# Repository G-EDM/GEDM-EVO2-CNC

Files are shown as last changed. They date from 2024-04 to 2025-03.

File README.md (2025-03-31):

# Schematics, Gerber files and Kicad projects for the PCBs
[>>> Schematics, Gerber files, Kicad projects and PCBway links <<<](https://github.com/G-EDM/GEDM-EVO2-CNC/tree/main/files/schematics-and-gerbers)
</br>
</br>

# GEDM-EVO2-CNC
Gantry based 3 axis CNC router with heavy duty 3d printed parts

```diff
  ______         ________ _______  __       __      ________ __     __  ______       ______ ______ 
 /      \       |        \       \|  \     /  \    |        \  \   |  \/      \     |      \      \
|  ▓▓▓▓▓▓\      | ▓▓▓▓▓▓▓▓ ▓▓▓▓▓▓▓\ ▓▓\   /  ▓▓    | ▓▓▓▓▓▓▓▓ ▓▓   | ▓▓  ▓▓▓▓▓▓\     \▓▓▓▓▓▓\▓▓▓▓▓▓
| ▓▓ __\▓▓______| ▓▓__   | ▓▓  | ▓▓ ▓▓▓\ /  ▓▓▓    | ▓▓__   | ▓▓   | ▓▓ ▓▓  | ▓▓      | ▓▓   | ▓▓  
| ▓▓|    \      \ ▓▓  \  | ▓▓  | ▓▓ ▓▓▓▓\  ▓▓▓▓    | ▓▓  \   \▓▓\ /  ▓▓ ▓▓  | ▓▓      | ▓▓   | ▓▓  
| ▓▓ \▓▓▓▓\▓▓▓▓▓▓ ▓▓▓▓▓  | ▓▓  | ▓▓ ▓▓\▓▓ ▓▓ ▓▓    | ▓▓▓▓▓    \▓▓\  ▓▓| ▓▓  | ▓▓      | ▓▓   | ▓▓  
| ▓▓__| ▓▓      | ▓▓_____| ▓▓__/ ▓▓ ▓▓ \▓▓▓| ▓▓    | ▓▓_____   \▓▓ ▓▓ | ▓▓__/ ▓▓     _| ▓▓_ _| ▓▓_ 
 \▓▓    ▓▓      | ▓▓     \ ▓▓    ▓▓ ▓▓  \▓ | ▓▓    | ▓▓     \   \▓▓▓   \▓▓    ▓▓    |   ▓▓ \   ▓▓ \
  \▓▓▓▓▓▓        \▓▓▓▓▓▓▓▓\▓▓▓▓▓▓▓ \▓▓      \▓▓     \▓▓▓▓▓▓▓▓    \▓     \▓▓▓▓▓▓      \▓▓▓▓▓▓\▓▓▓▓▓▓
```

# Downloadlinks for the freecad files
    The router file is a little crappy. The extrusions/tank/rails of the frame are not a the correct position and the Y ballscrew is too short etc.
    But it can be used

[>>> G-EDM EVOII Wire extension FreeCAD Project <<<](https://drive.google.com/file/d/1ZBrTBwRvTHIMtCySQIoWtpVMdJbfWR3E/view)
</br>
[>>> G-EDM EVOII Router FreeCAD Project <<<](https://drive.google.com/file/d/1OkYVYsVrToy4-q0G6XMzgWKsSyYXRRj4/view)
</br>
</br>

# Responsible for the content provided
    Lautensack Roland (Germany)
    Contact: goblin-dev@proton.me

# This project is still a work in progress and not fully finished yet

The GEDM-EVO2 Gantry Router uses heavy duty 3D printed parts, strong HGR20 linear rails, ballscrews and heavy profiles (40x160).

With only a few upgrades/changes it will be able to not only do EDM but also mill wood and smaller aluminum parts.

In order to do those milling jobs it may require a second ballscrew on the left side.

The wire extension used in the images is the one designed by Alex Treseder for the PicoEDM:
https://github.com/alextreseder/picoEDM

Not fully finished. Z axis is still missing and the massive aluminum plate on the front is temporary.

Check out the youtube channel:
Cutting stainless steel demo (https://youtu.be/4GycnoLOGnc)

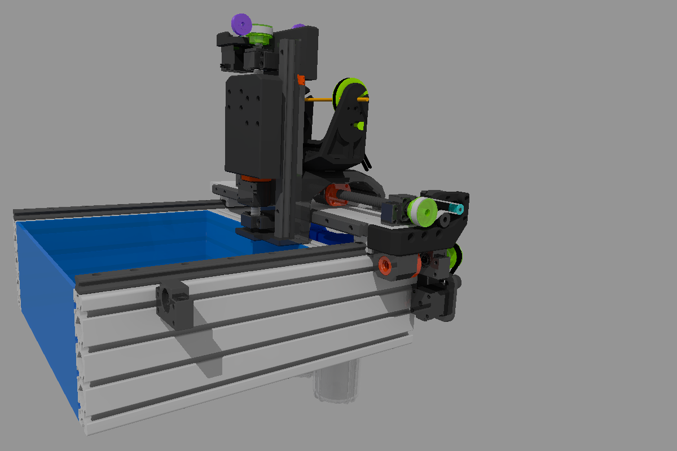
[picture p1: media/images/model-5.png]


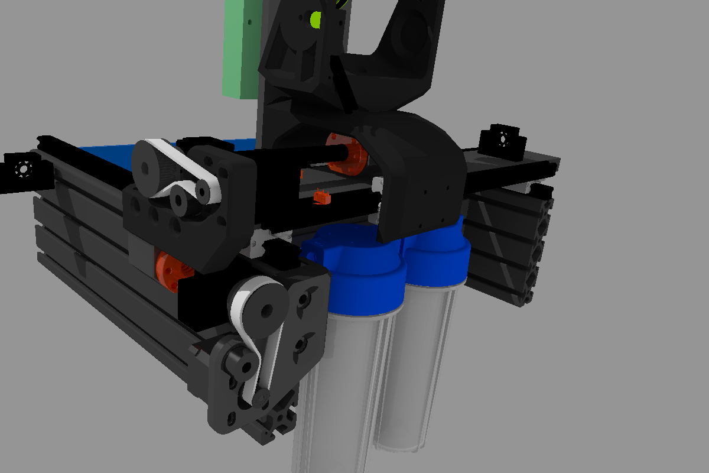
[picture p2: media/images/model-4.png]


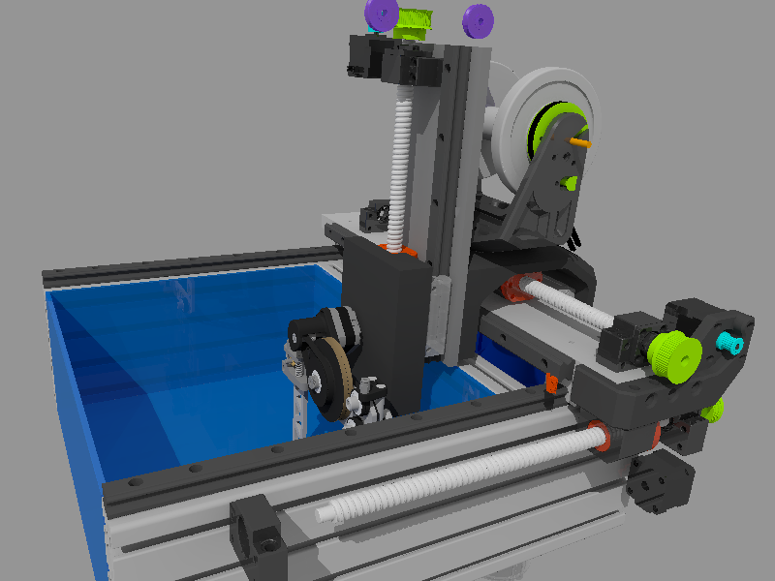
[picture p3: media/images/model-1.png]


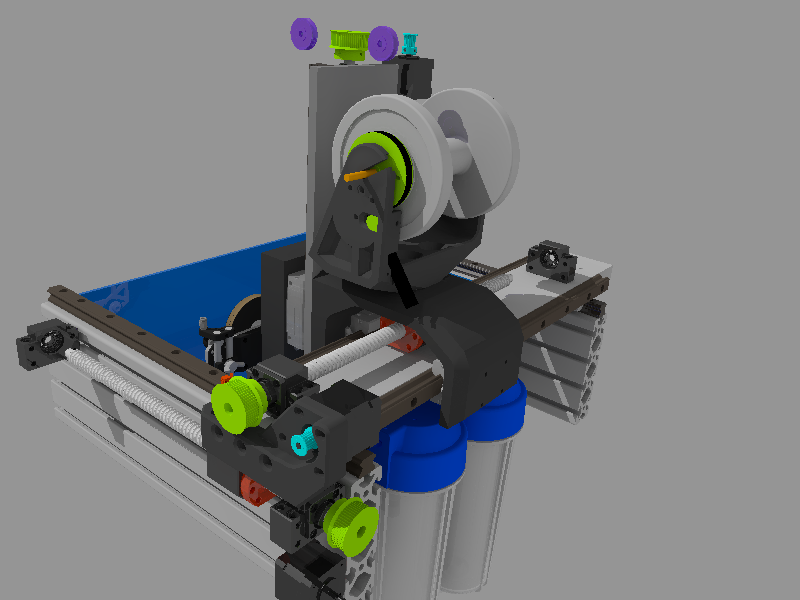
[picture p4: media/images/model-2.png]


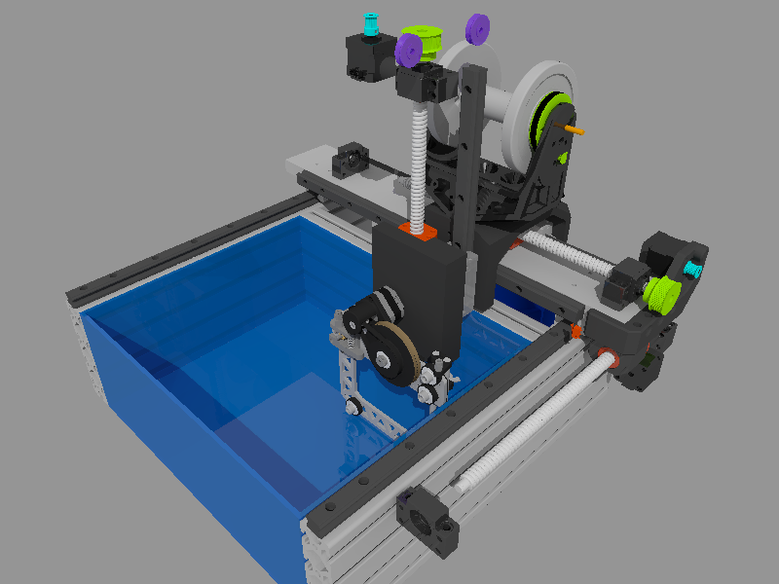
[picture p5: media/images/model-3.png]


# Legal notes

    The author of this project is in no way responsible for whatever people do with it.

    No warranty. 

# License

    All files provided are for private use only if not declared otherwise and any form of commercial use or redistribution of the protected files is prohibited. 

# Follow the project:

[>>> Follow the project on Youtube <<<](https://www.youtube.com/@G-EDM/videos)

[>>> Stay informed on Hackaday <<<](https://hackaday.io/project/190371-g-edm)

[>>> Get involved on Discord <<<](https://discord.gg/9cTsyDkEbe)

# Donations

    * Developement is not always as fast as it could be if you're poor. You want to donate something? 
    * Paypal: paypal.me/gedmdev
    * Bitcoin: bc1qkz8vwrd3pupewdtyg09qj9nv249vlgdy4ffhyv
    


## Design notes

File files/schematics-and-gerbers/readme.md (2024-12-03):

# Update

Added the new EVOIII PCB. This board was designed for easier manufacturing and is a replacement for the sensorboard and the pulseboard. It has both integrated on a single PCB.

The PCBs can be ordered on PCBway using following links:

# Motionboard
https://www.pcbway.com/project/shareproject/G_EDM_Low_budget_DIY_Wire_EDM_machine_34e1e043.html

# EVOIII Board (Sensorboard and Pulseboard on one PCB)
https://www.pcbway.com/project/shareproject/G_EDM_EVOIII_board_Low_budget_DIY_Wire_EDM_machine_482d5b7a.html

<br/><br/><br/><br/>
# If the EVOIII board is used the following two PCBs are not needed.
<br/><br/>

# Sensorboard (Not needed if the EVOIII board is used)
https://www.pcbway.com/project/shareproject/G_EDM_Low_budget_DIY_Wire_EDM_machine_sensorboard_24b74366.html

# Pulseboard (Not needed if the EVOIII board is used)
https://www.pcbway.com/project/shareproject/G_EDM_Low_budget_DIY_Wire_EDM_machine_pulseboard_8975f488.html

The full electronic enclosure contains the control panel with the ESP32 motion controller and a touch screen and the spark generator.

The pulseboard and the sensing unit are two dedicated PCBs stacked on top of eachother.

The sensing unit is not bound to the G-EDM pulseboard and can be used with a custom generator as well.

Currently only the schmeatics of the pulseboard PCB is uploaded here.

Sennsing unit / motionboard and gerber files will follow.

The pulseboard can be used as stand-alone board too but the sensing is not comparable to the new sense circuit that is able to capture raw watercontact and even the tiniest discharges.

Files currently provided:

Schematics:
```diff
+ Pulseboard EVO² - yes
```
```diff
+ Sensing Unit EVO² - yes
```
```diff
+ Motionboard EVO² - yes
```

Gerber files:
```diff
+ Pulseboard EVO² - yes
```
```diff
+ Sensing Unit EVO² - yes
```
```diff
+ Motionboard EVO² - yes
```

BOM:
```diff
+ Pulseboard EVO² - yes
```
```diff
+ Sensing Unit EVO² - yes
```
```diff
+ Motionboard EVO² - yes
```

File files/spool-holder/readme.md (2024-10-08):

# Note

The belt dampener doesn't work very well. The belt starts to increase tension over time and the spool motion is not smooth.

But there is an easy fix for now:

1. Fully remove the belt
2. Add one washer+lockwasher+washer to each side of the screws holding the spool (left/right)
3. Adjust the tension using those screws

Also mount the spool flipped by 180° and bring the spool more forward by skipping the back mounting screw row and only use the two front screws to mount it.

Images: https://github.com/G-EDM/GEDM-EVO2-CNC/tree/main/files/spool-holder/images/spool-bug-fix

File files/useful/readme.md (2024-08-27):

# Adapters to mount the shunt to the cube
# Little drill helper with the hole pattern of the cube

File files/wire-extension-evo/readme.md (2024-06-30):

The current contact I use is this one:
[EDM Maschine für S010-1 ](https://www.ebay.de/itm/276514273684)

40mm x 10mm x 5mm
https://de.aliexpress.com/item/1005007089428164.html

There are multiple screw holes that can be used to mount other contacts too or build a custom contact.

How to build it:
https://www.youtube.com/watch?v=NhJeJGdWdE0

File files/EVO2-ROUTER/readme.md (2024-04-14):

# Work in progress

This folder is not complete and may miss some files.

Missing files are mostly Z axis and build tutorial related.

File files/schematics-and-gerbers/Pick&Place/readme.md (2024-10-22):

# WARNING!!!

This is currently a work in progress to provide files for PCBA (Assembly) services.

It is not finished yet and needs validation and testing first.

The BOMs only contain the SMD parts and not the through hole parts.

There are some problems figuring out the correct footprints for the ICs. Every manufacturer names things different and it is a total mess.
In the end there are all kinds of footprints labeled as for example SOP-8 but have massive difference in size.
Then there is SOIC-8 which seems to be the same as "some" SOP-8 etc.

Industry messed this up badly and I have to sort this out first.

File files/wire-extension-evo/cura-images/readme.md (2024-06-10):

The support settings shown are just the ones I used. Printer is an Ender3 v2 with MGN12 linear rails and BLtouch sensor for auto bed leveling.

The printposition of the parts needs to be as shown on the images.

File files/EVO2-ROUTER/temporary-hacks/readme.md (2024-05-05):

# This is just a temporay solution 

The files included in this folder are personal hacks to get the wire extension mounted without using the final Z axis. This folder will be removed once everything is finished!

It is not perfect but it will get some stuff done.

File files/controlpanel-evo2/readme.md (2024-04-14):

This folder includes the raw freecad project file for the panel too.

# License

    All files provided are for private use only if not declared otherwise and any form of commercial use or redistribution of the protected files is prohibited. 

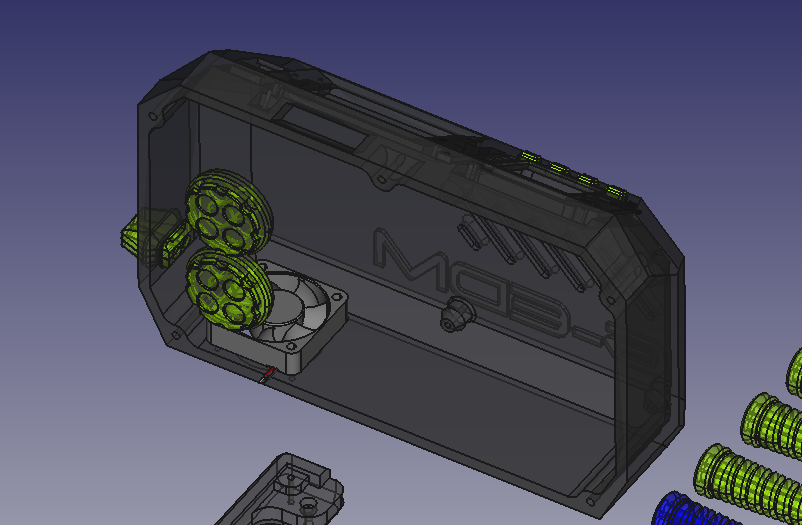
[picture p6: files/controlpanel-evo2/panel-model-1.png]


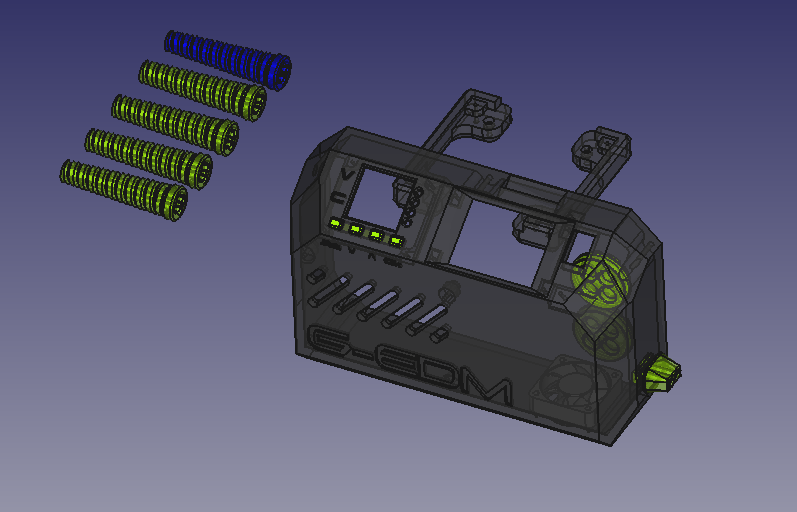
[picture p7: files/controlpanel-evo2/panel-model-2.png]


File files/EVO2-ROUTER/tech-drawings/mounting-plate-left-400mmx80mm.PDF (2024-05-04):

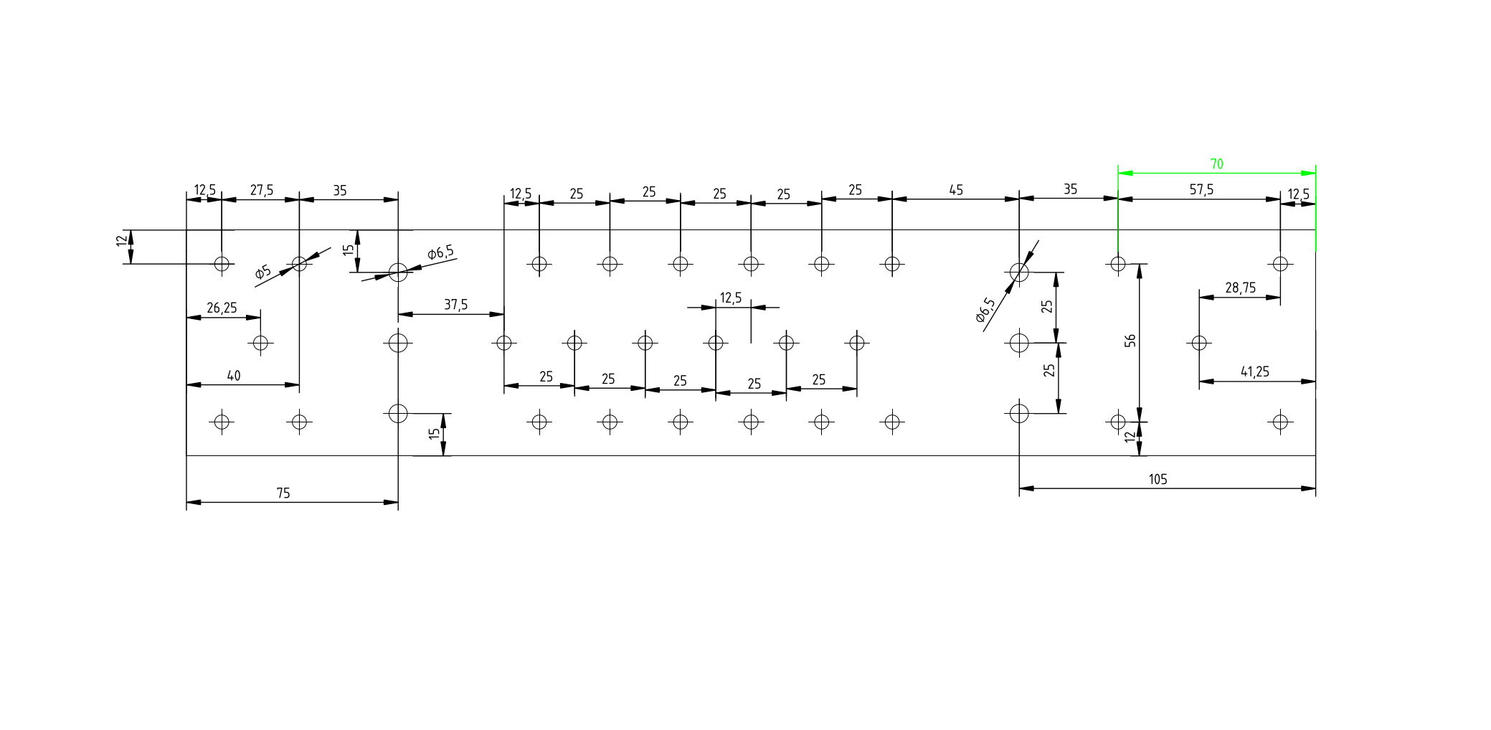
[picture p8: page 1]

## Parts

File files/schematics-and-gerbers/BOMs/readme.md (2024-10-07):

# Warning:

No warranties. The BOMs may contain errors or miss parts. I have done them really quick without deeper review.

Some parts of the BOM are using the discount price if 10 pieces are bought. Nobody buys 1 0805 SMD resistor etc.

Sensorboard: 57,17.- (Euros)
Motionboard: 13,80.-
Pulseboard: 41,25.-

112.25.- for the PCB components without taxes. 
134.65 with tax

PCBway has a minimum order of 5 PCBs per board. A full set ordered from PCBway would contain:
     5 Motionboards
     5 Sensorboards
     5 Pulseboards

Cost with tax and shipment for the 15 PCBs:
     175.77.- (Euros)

Per Set (One of each boards):
     35.154.-
     
Total for One populated Set of boards:
    169.80.-

Other parts needed: JST male connectors, wires etc are not calculated yet. 
ESP32 and TMC drivers are not included in the motionboard BOM

There are other parts needed like:

M3 Hex spacer M3*26mm
https://www.ebay.de/itm/166217190652

M3 Washers and screws

22AWG silicone wire black/red

JST XH crimpset

And maybe some other stuff. Read the manual:
https://www.youtube.com/watch?v=dQw4w9WgXcQ

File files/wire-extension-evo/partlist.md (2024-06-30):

This partlist is a work in progress and may miss some parts like the exact amount of washers and maybe a screw too. The small V bearings may need two washers to prevent them from rubbing. They are not build very rigid and have some play. 

##### Tools #####
M10 tap (to make the thread for the flushing tube fittings)
An Allen Wrench set 
10mm hex nut key (to screw the flushing fitting in)
A small micro gas blow torch to postprocess some of the printed parts. Remelting outer layers and screwholes to make them more solid.

If possible use stainless screws/nut/washers. Normal steel will rust fast.

##### Filament #####
2 spools PLA+ (eSun is very good)
A few grams TPU to print the flushing nozzle seals

##### Current contact #####
    The are different holes that can be used to mount other/custom contacts too.
    S010-0 current contact; 40mmx10mmx5mm
    https://de.aliexpress.com/item/1005007089428164.html
    https://www.ebay.de/itm/276514273684

##### Screws #####

     ### M3 ###  
     4x M3x12mm (for spool motor) 
     2x M3x14mm 
     2x M3x18mm (20mm is ok too)
     1x M3x20mm
     2x M3x25mm
     2x M3x30mm
     2x M3x5mm setscrews (8mm length is ok too)

     ### M5 ###
     6x M5x30mm
     2x M5x35mm
     2x M5x8mm setscrew (can be longer too)

     ### M6 ###
     1x M6x25mm
     2x M6x30mm 
     2x M6x35mm
     3x M6x40mm
     2x M6x50mm
     3x M6x55mm (60mm works for those too)
     4x M6x60mm

##### Hexnuts #####

    12x M3
    10x M5
    14x M6
    
    ##### selflocking #####
    1x M3
    3x M6

##### Washers #####

    11x M3
    6x M5
    14x M6

##### Slide bearings #####

    4x 12mm OD x 10mm ID x 10mm Length
    https://www.amazon.de/sourcing-map-Gleitlager-umwickelte-%C3%96lbarren/dp/B07KQ5RSJW

##### Bearings #####

The big bearings body is from stainless and will not rust but the balls inside will rust very fast. After the first use the bearings have water inside and it takes only one or two days for the bearing to fully block if not moved daily. It is ok to remove one ball from the bearings. Even if the bearings will have a little play it prevents them from getting stuck. The best way is to replace the balls with ceramic balls. This combination would last very long.

3x V623ZZ 3x12x4mm bearings (v-groove)
https://www.amazon.de/St%C3%BCck-V623ZZ-V-Nut-Kugellager-Riemenscheibe-Schienen-Linearbewegungssystem-3x12x4mm/dp/B08K95KNFR

7x 696-2RS Kugellager sealed 6x15x5mm 
https://www.amazon.de/dp/B09V5DBM6Y

5x v groove bearing "Cnbtr" 6x30x8mm (2.5mm groove depth. They are sold as 8mm width but the center is 9mm and only the outer ring is 8mm. Integrated washers)
https://www.amazon.de/dp/B076VCCCMS

##### Rails #####

2x 10mm x 180mm precision roundbar in stainless steel
https://www.amazon.de/Pr%C3%A4zisionswelle-10mm-geschliffen-geh%C3%A4rtet-ZUSCHNITT/dp/B07GNG1Y3Z

##### Others #####

1x small Banana plug socket with M6 thread (The little panel can be modified to fit other sockets too)

2x Pneumatic fittings with M10 thread
https://www.amazon.de/dp/B07DGLCJ4Z

2x V5/V6 3D printer nozzle in stainless steel or tungsten with the size of the wire
https://www.amazon.de/PREMIUM-Nozzle-0-25mm-Edelstahl-Stainless/dp/B0CNWG1KYZ

##### Not specified yet #####

1x banana socket
2x springs
4mm OD hydraulic tube
EDM current contact

##### Printsettings #####

Print inner walls first!

Most parts have supports touching buildplate only. This is important for the big main body and the upper/lower guides as there is no way to remove the supports from the internal routing. Printing throughholes and hexnutslots with the edge to the top works without problems.

The big parts should have supports on the outer chamfers too while this is not needed for smaller parts. So some parts have a support angle <45° while the ones that don't need chamfer supports do ha ve a support angle >45°. For the parts without chamfer supports just set it to 50°.

The motor shaft is printed without any supports. 

Postprocessing:

There are four parts that need heat postprocessing to increase the strength. The wire tensioner A and B and the wire follower and alos the motor shaft.

The motor shaft is easy to refine. First insert the hexnuts. The heating will shrink the part. 

Put a screw into it, plug it onto a drill and heat it up. Step by step. First the circular/smooth area, then cool it with water, Then the middle torque connection area and again cool it and then a tiny sensitive and short heating on the thread. Really just a super short amount of time.

After that use sandpaper to smoothen the circualr area. Rough grid and then fine grid. Then use a M5 screw to enlarge the hole for the stepper shaft. Using a screw seems to be more carefully then a drill. The thing should sit tightly on the stepper even without the setscrew locking it.

Same heattreatment for the wire tensioners and wire follower. Put the bearings in first to prevent shrinking and then do the outer part. A little deformation is ok. Those parts don't need high precision. Don't do the full part in one pass. Step by step and leting it cooldown again between steps.

If the plastic burns or smokes it is done wrong. There are two ways. One is to move the ligther fast and constant to slowly heat the area. But this will certainly burn the part sometimes. Another is to place the part close to the side of the flame until it gets glossy. This works with a normal lighter too and will give a nice result without much risk for overheating but will take much more time to make.

Printsettings for the big wire module (main body and connector):

Those settings will create a harder to remove support structure! Postprocessing will take more time.
This settings are only used for heavy duty parts.
Add a thick layer adhesive to the Ender3v2 printbed. I used hairspray but that may not work for everyone.. Use an adhessive that works for the build plate of the printer.

Layer height: 0.3mm
Walls: 14 (wall print order: inner walls first for better overhangs)
Top/Bottom layers: 12
Temperature: 230° for eSun PLA+

Print Speed: 50mm/s (Warning: Those are the settings I used to create the gCode. But I changed the speed on the printer to 80% of those settings)
    Infill: 50mm/s
    Outer Walls: 25mm/s
    Inner Walls: 30mm/s
    Top/Bottom: 35mm/s
    Support Infill: 25mm/s
    Support Interface: 35mm/s
    Travel Speed: 100mm/s
    Brim: 20mm/s

Infill: 
    Density: 70% 
    Pattern: Lines
    
Support:
    Structure: Normal
    Placement: Touching Buildplate
    Overhang Angle: 20°
    Pattern: Lines
    Density: 20%
    Z-Distance: 0.2mm
    X/Y Distance: 0.3mm
    Priority: Z overrides X/Y
    Enable Support INterface: All yes
    Support Interface Thickness: 2mm for all
    Support Interface Density: 26.333%
    Support Interface Pattern: Lines
    
Adhesion:
    Build Plate Adhesion Type: Brim
    Brim Width: 12mm
    Brim Replaces Support: Yes

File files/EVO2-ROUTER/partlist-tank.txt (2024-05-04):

Acrylic glass:
    1x 430x429x8mm
    2x 420x152x5mm
    2x 429x152x5mm
    
    4x 50x50x50mm acrily block to mount the stainless plate (Warning: The blocks are cutted from a thick plate/bar and the sides that are cut are most fo the time not accurate. Measure the block to find the accurate top/bottom. )
    
Glue:
    1x Solvent (S-PolyBond® or similar. Viscosity like water)
    1x Glue (Acrifix 1R 0192 or similar. Thicker glue fro acrylic used to seal the inner edges. Acrifix 0192 is UV reactive. It smells like hell and without a UV lamp it takes long to harden. A small UV pocket lamp is ok. If no UV lamp is available put the part into the sun. It does dry with room light too but takes very long and keeps smelling everything up. Acrifix 0190 is the non UV version.)

Stainless steel plate:
    1x 400x80x6mm

Fittings for the hose:
    2x 3/4" Female 1" Male Brass Bulkhead Fitting
    1x 3/4" 13mm barbed brass hose fitting with outer thread (screwed into the big fitting)
    
    In germany there are sets available: https://www.ebay.de/itm/193008996748
    
Hose:
    12mm ID hose.
    
Pump:
    12v pump, 1000l/min, 30w https://www.amazon.de/gp/product/B0C3Q887C5
    The pump in the link does not ship with hose fittings! If you get this specific model it needs two 1/2" barbed fittings with inner thread.

Filter:
    2 stage RO water filter. One stage with an activated carbon filter and the other sage with a 5 micron sediment filter.
    https://www.amazon.de/Naturewater-Wandhalterung-Filterschl%C3%BCssel-Sedimentfilter-Aktivkohleblock/dp/B008U8BY90
    
    Depending on the filter you buy it may need another set of barbed fittings. This time with outer thread.

Build tips:

    Using the watery solvent is not easy. Good luck.
    
    I used the solvent to get the box together and then just poured solvent into the inner edges while having the box tilted. This way the solvent will suck into the joint where the connection is not done. Don't wait with this too long and do this as soon as the box can be moved without falling apart which happens fast.

    If the solvent drops onto the acrylic don't wash it away. Let it vaporize! It will leave cloudy marks that later can be get rid of with a small lighter blow torch. Just blow torch it with a constant motion until it is transparent again. Same can be done with the edges of the box.
    
    One thing to keep in mind while flame polishing acrylic is that it creates stress in the plate. If solvent touches a flame polished surface it will instantly start to create cracks in the surface. In theory it is better not doing it and keep the milky spots.
    
    Using some sandpaper to round the edges and then blowtorch them shiny.

    After the solvent vaporized and the box is stable the inner joint needs to be sealed. Tilt the box and fill the joint with the glue in a straight line. Let it crawl into the joint, give it some time to rest and then go one to the next edges. Process is repeated multiple times to have a strong and thick seal on every joint. Give it a little time between each pass to let it dry a little bit.

    To drill the big hole I used a step drill bit and some smaller drills to predrill the initial hole.
    
    The step drill bit was a little too small so after having the main hole drilled I placed the fitting into the hole and used the small blow torch to heat it up until it started to soften the plastic. Do this carefully and step by step.
    
    After the fitting is in place remove the plastic from the edges and clean the hole.
    
    To get a really flat surface insert the fitting without gaskets, screw it tight and then heat the fitting from the inside again. It will align itself in place.
    
    Remove the hot fitting as soon as possible and also use a large M8 hex key to work with the hot fitting and prevent it from tilting.

    The brass fitting will be too hot to handle with bare hands and it will take long until it cools down.

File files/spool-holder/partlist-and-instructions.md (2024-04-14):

1x M4x16
1x M6x35
1x M6x45
2x M3x40 (min 30mm)
1x M3x16
2x M3x20 (larger is ok too)

2x Hexnut M6 (self locking! Important!)
2x Hexnut M3

Ballbearing 15x6x5 (OD 15mm; ID 6mm; 5mm height)

6mm GT2 belt (open ended)

Print tips:

Spool holder main can be printed with 25% infill and 5 walls.
It is a big part and it is highly recommended to add some adhesive to the build plate. I use 
strong hairspray. Lots of it.

All other PLA+ parts are printed with 100 infill.

The TPU ring is printed with 1 wall and 20% infill to keep it soft.

Build tips: 

Use a stormlighter to heat screws and screw them in hot where needed to create the threading. Same process sued for hexnuts too. 

It is also recommended to carefully use a stormlighter on the big part and re-melt the outer layers at critical position. Needs to be done carefully and fast to not burn the plastic or create burned spots. This increases the average strength heavily.

If the adapter is hard to put into the spool just put an M6 screw into a drill, screw the adapter on it and sand it down until it fits.

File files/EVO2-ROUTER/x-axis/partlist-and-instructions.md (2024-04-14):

1x 500mm 1605 SFU ballscrew with SF12 / SK12 bearing blocks and a DSGH16H nut housing
2x 500mm HGR20 linear rail
2x HGH20CA linear block

Note: Most sets of linear rails ship with 2 blocks per rail. We don't need to blocks per rail and it is possible to just take one 1000mm rail with two block and cut it into two 500mm rails.

1x Aluminum plate 600mm x 85mm x 20mm (best is to have grinded surface and a precision cut; The cut needs to be very very parallel!)

1x M3 to M6 flat washers and lock washers (a set or jsut a bunsh of them for eevery size)

Screws:

4x M6x30mm (To mount the spoolholed onto the slide)
4x M5x12
8x M5x20
4x M3x (to mount the Nema17)
1x M8x (to mount the belt tensioning bearings)
2x M3x12 (to tighten the big pulley)
2x M3 setscrew (to tighten the small pulley)
3x M6x (to mount the motor bracket onto the portal plate)
1x M5x (to mount the motor bracket onto the portal plate)

2x M6x (for the BF12) // If you don't have good tools and use a hand drill I recommend to mount those bearings with M5 instead of M6. Using M5 gives some more room for misalignment while drilling)
4x M6x (for the BK12) // If you don't have good tools and use a hand drill I recommend to mount those bearings with M5 instead of M6. Using M5 gives some more room for misalignment while drilling)

4x M5x (for the DSGH16H)

Hex Nuts:

A bunsh of M6 hex nuts (just a few, maybe 10)
A bunsh of M3 hex nuts (just a few for the pulleys needed. Maybe 4)

2x Ball bearings 608ZZ 8mmx22mx7mm (height can be more than 7mm too. Even with two bearings it is a tight fit for the belt on the edge.)

10mm GT2 belt (closed; length not determined yet)

Print tips:

The big XZ slide needs to be printed laying on the left side. Normal supports touching buildplate only and 30° support overhang angle.
A Brim is also needed. I used a 15mm Brim.
Another important thing is to spray the printbed with some kind of adhesive. Strong hairspray works for Ender3v2 printbeds. A lot of it.

The part is heavy duty and consumes almost an entire spool. Travelspeed should be reduced. My ender is modified with MGN12 lienar rails and used 110mm/min for travels. 
Layerheight can be 0.3mm. My print took <50 hours.

Build tips:

After the part is finished it is recommened to increase the average strenght with the help of remelting.
At least the holes need to be remeleted. Bolting M6 screw tightly can easily split the layer apart. To do so just use a small blowtorch and heat up the inner holes.

I remelted the full outer part but this will shrink the part heavily and needs to be done carefully.

Mount the part first to prevent the shrinking from respotioning the holes etc too much. Then blowtorch along the part fast and until the surface gets glossy.
Don't do this with the full part at once. Surface after surface and in between letting it cool down.

To give it a nice matte finish the part can then get a little sanding.

Some holes may need to be drilled to size after printing and if something does not fit well it is possible to use a soldering iron to change the hole positions.

If there is too much resistance in the ballscrew it is also possible to soften the back and/or top of the slide to release the stress and force it into a perfect fit.

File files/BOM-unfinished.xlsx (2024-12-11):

 |  | G-EDM BOM Extra
Item # | *Qty | Manufacturer | *Mfg Part # | Description / Value | Comments | Euros total
1 | 1 |  | ILI9341 Touch Display; SPI; 2,4“; 240x320; XPT2046 (Touch controller); | There are many different version available. Those two fit in the panel and work: https://www.amazon.de/ILI9341-240x320-Display-Touch-Arduino/dp/B07YTW28FB https://www.ebay.de/itm/145884439469
2 | 2 | Az-delivery | ESP32 NodeMCU Module WLAN WiFi Development Board | Dev Kit C V2 with CP2102; 38 Pins | https://www.az-delivery.de/en/products/esp32-developmentboard
3 | 1 |  | On/Off rocker switch; 2 pole; Normally Open; 9x13mm | https://www.amazon.de/Mini-Wippenschalter-Wippschalter-Kippschalter-Ger%C3%A4teschalter-rechteckig/dp/B0CCCBLXCS
4 | 4 |  | ST42STH47-1684A | Nema 17; 0.4Nm; 1.68A; 1.8° Step angle; Rated 2.8v; https://eu.robotshop.com/de/products/nema-17-schrittmotor-sy42sth47-1684a-einzelwelle |  | 88.-
5
6 | 1 |  | DPH8909 (TTL) | DPH8909 Programmable DC Power Supply CC CV TTL Communications Output 0-9.6A os12 https://www.ebay.de/itm/355082474892 | TTL version! Not the RS or RF version. The DPM8605 is half the price and works too but has a max output voltage of 60V and the input voltage needs to be set below 70V | 110.-
7 | 1 |  | 0-80V variable PSU; 6A480W | https://www.amazon.de/Transformator-Dual-Digital-Anzeige-Schaltnetzteil-Drehzahlregelung-wissenschaftliche/dp/B0BQ33XG33 |  | 56.-
8 | 1 |  | 12V 10A PSU | https://www.amazon.de/Kingwei-Schaltnetzteil-Netzteil-Transformator-Streifen/dp/B08QCNYLY8 |  | 18.-
9 | 1 | Mean Well | MEAN WELL PSU APV-35-12, 12 V-/3 A | https://www.amazon.de/MEAN-WELL-Schaltnetzteil-APV-35-12-12/dp/B083QNC9XG |  | 17.-
10 | 4 |  | TMC2209 Stepper driver with big heatsink | https://www.amazon.de/WANGCL-Schrittmotor-Treiber-K%C3%BChlk%C3%B6rper-hervorragende-Stummschaltung/dp/B0B1MM4BKH |  | 28.-

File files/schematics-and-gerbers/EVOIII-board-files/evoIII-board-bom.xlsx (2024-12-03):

 |  |  | G-EDM EVOII Sensorboard – BOM
Item # | *Designator | *Qty | Manufacturer | *Mfg Part # | Description / Value | *Package/Footprint | Type | Comments
16 | C31,C32,C23,C22 | 4 | KEMET | C0805C101J5RACTU | Multilayer Ceramic Capacitors MLCC - SMD/SMT 50V 100pF X7R 0805 5% | C_0805_2012Metric_Pad1.18x1.45mm_HandSolder | SMD
2 | C1,C3,C6,C8,C10,C13,C16,C18,C20,C27,C30,C35,C36,C37,C38,C39,C40,C45,C46 | 19 | KYOCERA AVX | 08055C104K4T2A | Multilayer Ceramic Capacitors MLCC - SMD/SMT 50V 0.1uF X7R | C_0805_2012Metric_Pad1.18x1.45mm_HandSolder | SMD
36 | C25,C24 | 0 |  | DNP | DNP | C_0805_2012Metric_Pad1.18x1.45mm_HandSolder | SMD | DNP
39 | C11,C29 | 2 | Murata Electronics | GRM32RR71H105KA01K | Multilayer Ceramic Capacitors MLCC - SMD/SMT 1 uF 50 VDC 10% 1210 X7R | C_1210_3225Metric_Pad1.33x2.70mm_HandSolder | THT
15 | C2 | 1 | KYOCERA AVX | 12107A101JAT2A | Multilayer Ceramic Capacitors MLCC – SMD/SMT 500V 100pF | C_1210_3225Metric_Pad1.33x2.70mm_HandSolder | SMD
4 | C28,C33,C44,C43 | 4 | Panasonic | EEEHA1C470WR | Aluminium Electrolytic Capacitors - SMD 16V 47uF | CP_Elec_5x5.4 | SMD
5 | C12,C15,C17,C21 | 4 | Panasonic | EEE-HAV221UAP | Aluminium Electrolytic Capacitors - SMD 220UF 35V | CP_Elec_8x10.5 | SMD
43 | C7 | 1 | Panasonic | EEE-HAC221XAP | Aluminium Electrolytic Capacitors - SMD 220UF 16V HA SMD | CP_Elec_6.3x7.7 | SMD
35 | R30,R31 | 2 | Vishay / Dale | RCC08050000Z0EA | Thick Film Resistors - SMD Zero ohm Jumper | R_0805_2012Metric_Pad1.20x1.40mm_HandSolder | SMD
9 | R4,R10 | 2 | Panasonic | ERJ-T06J221V | Thick Film Resistors - SMD 0805 220ohms 5% | R_0805_2012Metric_Pad1.20x1.40mm_HandSolder | SMD
20 | R11,R42 | 2 | KOA Speer | RK73B2ATTD561J | Thick Film Resistors - SMD 1/4watts 560ohms 5% | R_0805_2012Metric_Pad1.20x1.40mm_HandSolder | SMD
12 | R8,R9,R14,R15 | 4 | KOA Speer | RK73B2ETTD104J | Thick Film Resistors - SMD 1/2W 100Kohms 5% | R_1210_3225Metric | SMD
1 | R16,R17,R18,R19 | 4 | Vishay / Dale | RCC08051K00FKEA | Thick Film Resistors - SMD 1/4W 1Kohms 1% 100ppm | R_0805_2012Metric_Pad1.20x1.40mm_HandSolder | SMD
32 | R27,R26 | 2 | Vishay / Dale | RCC08054K70FKEA | Thick Film Resistors - SMD 1/4W 4.7Kohms 1% 100ppm | R_0805_2012Metric_Pad1.20x1.40mm_HandSolder | SMD
3 | R40,R41,R36,R37 | 4 | KOA Speer | RK73H2ARTTD2002F | Thick Film Resistors - SMD 1/4W 20K OHM 1% | R_0805_2012Metric_Pad1.20x1.40mm_HandSolder | SMD
19 | R24,R25,R38,R39 | 4 | Würth Elektronik | 560112120013 | Thick Film Resistors - SMD WRIS-RSKS 100 kOhms 1 % 0.25 W 0805 | R_0805_2012Metric_Pad1.20x1.40mm_HandSolder | SMD
23 | R2,R20,R21,R22,R23 | 5 | Würth Elektronik | 560112120004 | Thick Film Resistors - SMD WRIS-RSKS 10 kOhms 1 % 0.25 W 0805 | R_0805_2012Metric_Pad1.20x1.40mm_HandSolder | SMD
28 | R1,R28,R29 | 3 | Würth Elektronik | 560112120015 | Thick Film Resistors - SMD WRIS-RSKS 200 Ohms 1 % 0.25 W 0805 | R_0805_2012Metric_Pad1.20x1.40mm_HandSolder | SMD
34 | R3 | 1 | Vishay / Dale | CRCW12101K00JNEAIF | Thick Film Resistors - SMD 1kOhm 5% | R_1210_3225Metric | SMD
7 | R13,R12,R6,R7 | 4 | YAGEO | RC2512JK-7W4R7L | Thick Film Resistors - SMD 4.7 Ohms 2 W 2512 5% | R_2512_6332Metric_Pad1.40x3.35mm_HandSolder | SMD
13 | R5 | 1 | Panasonic | ERJ-U12F1001U | Thick Film Resistors - SMD 1812 1% 1.0Kohm | R_1812_4532Metric_Pad1.30x3.40mm_HandSolder | SMD
40 | D4 | 1 | Kingbright | APT2012LVBC/D | Standard LEDs - SMD 2.0X1.2MM LOW CRNT | LED_0805_2012Metric_Pad1.15x1.40mm_HandSolder | SMD
29 | D10,D9,D13 | 3 | Bivar | SM0805UGC | Standard LEDs - SMD Ultra Green 525 nm Water Clear, 20mA, 2v | LED_0805_2012Metric_Pad1.15x1.40mm_HandSolder | SMD
44 | D12 | 1 | Panjit | MB520_R1_00001 | Schottky Diodes & Rectifiers 200V,Schottky,SMC,5A | D_SMC_Handsoldering | SMD
31 | D14,D15 | 2 | Micro Commercial Components (MCC) | SMBJ5378B-TP | Zener Diodes 5W ZENERS SMB, 100V | D_SMB_Handsoldering | SMD
38 | D8,D5 | 2 | onsemi | 1N5378B | Zener Diodes 100V 5W | D_DO-201_P5.08mm_Vertical_AnodeUp | THT
25 | D1,D3,D6,D7,D18,D19 | 6 | Vishay General Semiconductor | B360A-E3/61T | Schottky Diodes & Rectifiers 60 Volt 3.0 Amp 50 Amp IFSM | D_SMA_Handsoldering | SMD
26 | IC12 | 1 | Texas Instruments | INA293B3 | Current Sense Amplifiers AEC-Q100, -4-V to 110-V, 1.3-MHz, ultra-precise current sense amplifier 5-SOT-23 -40 to 125 | SOT95P280X145-5N | SMD
30 | IC11 | 1 | onsemi | MC7805CDTRKG | Linear Voltage Regulators 5V 1A Positive | MJD1221G | SMD
6 | IC1,IC13,IC2,IC8 | 4 | Texas Instruments | OPA350UA | High Speed Operational Amplifiers Hi-Spd Single-Sply Rail-to-Rail | SOIC127P600X175-8N | SMD
10 | IC5 | 1 | Lite-On | 6N137S | High Speed Optocouplers High Speed 10MBd LogicGate Output | SOP254P1016X460-8N | SMD
11 | IC6,IC7 | 2 | Broadcom / Avago | HCNR201-500E | High Linearity Optocouplers 1 Ch 60mW 25mA | SOP254P1230X400-8N | SMD
17 | IC4,IC3 | 2 | ROHM Semiconductor | LM358F-GE2 | Operational Amplifiers - Op Amps Dual Grnd Sense Op Amp SOP8 | SOP-8_3.9x4.9mm_P1.27mm | SMD
33 | IC9 | 1 | IXYS Integrated Circuits | IXDI609CI | Gate Drivers 9-Ampere Low-Side Ultrafast MOSFET inverting | IXDI609CI | THT
21 | J20 | 1 | Weidmüller | 8000078309 | Pluggable Terminal Blocks PCB plug-in connector (board connection), 7.50 mm, Number of poles: 4, Outgoing elbow: 90 | 8000078309 | THT
22 | J20 | 1 | Weidmüller | 8000078355 | Pluggable Terminal Blocks MPS 7S/04 S F2 TN B B
8 | J4 | 1 | JST Commercial | S2B-XH-A(LF)(SN) | JST Automotive Connector | JST_XH_B2B-XH-A_1x02_P2.50mm_Vertical | THT
14 | J13,J17,J1 | 3 | JST Commercial | B2B-XH-A(LF)(SN) | CONN HEADER VERT 2POS 2.5MM | JST_XH_B2B-XH-A_1x02_P2.50mm_Vertical | THT
37 | J16 | 1 | JST Commercial | S5B-XH-A(LF)(SN) | JST Automotive Connector | JST_XH_S5B-XH-A_1x05_P2.50mm_Horizontal | THT
41 | J2,J9 | 2 | TE Connectivity / AMP | 1776138-2 | Pluggable Terminal Blocks 2P TERMI-BLOK HDR HIGH TEMP (board connection) | CONN2_796643-2_TEC | THT
42 | J2,J9 | 2 | TE Connectivity / AMP | 796641-2 | Pluggable Terminal Blocks 2 POS 5.0 MM R/A PLUG TRM BLK | CONN2_796643-2_TEC | THT
27 | C9 | 1 | WIMA | FKP2F004701D00JSSD | Film Capacitors 250V 470pF 5%, 5mm lead spacing | FKP2F004701D00JSSD | THT
24 | C5 | 0 |  | DNP | DNP | C_1206_3216Metric_Pad1.33x1.80mm_HandSolder | SMD | DNP
45 | C4 | 0 |  | DNP | DNP | CP_Radial_D14.0mm_P5.00mm | THT | DNP
46 | D2 | 1 |  | DNP | DNP | D_SOD-123F | SMD | DNP
47 | RV5 | 1 | Bourns | 3296Y-1-103LF | Trimmer Resistors - Through Hole 3/8" 10Kohms Sealed Vertical Adjust | Potentiometer_Bourns_3296Y_Vertical | THT
48 | PS1 | 1 | RECOM Power | RS3K-2405SZ/H3 | Isolated DC/DC Converters - Through Hole 3W 9-36Vin 5Vout 600mA | RS3K2405SZH3 | THT
51 | Q3,Q2,Q4,Q1 | 4 | Infineon Technologies | IRFP260NPBF | MOSFETs MOSFT 200V 49A 40mOhm 156nCAC | TO-247-3_Horizontal_TabUp | THT
52 |  | 1 | FISCHER ELEKTRONIK | SK508-100SA | Heatsink; 100 x 25 x 100 mm |  |  | DNP
53 |  | 1 | ALUTRONIC | SI 6018 | Silicone isolation foil; 20x94x0,18 |  |  | DNP
54 |  | 4 | FISCHER ELEKTRONIK | IB 16 | Isolation bushing, M3 |  |  | DNP
55 |  | 4 |  | M3x20 screw with hexnut |  |  |  | DNP

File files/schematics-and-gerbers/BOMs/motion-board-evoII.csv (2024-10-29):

Bezeichner | Footprint | Stückzahl | Bezeichnung | Anbieter und Referenz |  |  | Price pre piece in Euro | Total | Datasheets
C2,C3,C7,C8,C11,C12,C13,C14,C15,C16,C17,C18,C19,C20,C24,C26,C27 | C_0805_2012Metric_Pad1.18x1.45mm_HandSolder | 17 | 0.1uf-50v-x7r 08055C104K4T2A | 08055C104K4T2A |  |  | 0,053 | 0,901
C22 | C_1210_3225Metric_Pad1.33x2.70mm_HandSolder | 1 | 4.7uf-50v-X7R GRM32ER71H475KA88L | GRM32ER71H475KA88L |  |  | 0,791 | 0,791
C21 | C_1210_3225Metric_Pad1.33x2.70mm_HandSolder | 1 | 22uf-16v-X7R GRM32ER71C226KEA8K | GRM32ER71C226KEA8K |  |  | 0,409 | 0,409
C1,C4,C9,C10 | CP_Elec_6.3x7.7 | 4 | 100uf35v-6.3x7.7mm EEE-HA1V101XP | EEE-HA1V101XP |  |  | 0,214 | 0,856
C6,C5 | CP_Elec_6.3x7.7 | 2 | 220uf16v-6.3x7.7mm EEE-HA1C221XP | EEE-HA1C221XP |  |  | 0,233 | 0,466
 |  |  |  |  |  |  |  | 0
 |  |  |  |  |  |  |  | 0
R8,R13 | R_0805_2012Metric_Pad1.20x1.40mm_HandSolder | 2 | 330 Ohm 1% RCC0805330RFKEA | RCC0805330RFKEA |  |  | 0,071 | 0,142
R7,R10,R14 | R_0805_2012Metric_Pad1.20x1.40mm_HandSolder | 3 | 470 Ohm 1% RCC0805470RFKEA | RCC0805470RFKEA |  |  | 0,041 | 0,123
R1,R2,R4,R6,R12 | R_0805_2012Metric_Pad1.20x1.40mm_HandSolder | 5 | 100 kOhm 1% WRIS-RSKS 560112120013 | WRIS-RSKS 560112120013 |  |  | 0,052 | 0,208
R9 | R_0805_2012Metric_Pad1.20x1.40mm_HandSolder | 1 | 499 Ohm 1% MR08X4990FTL | MR08X4990FTL |  |  | 0,039 | 0,039
R3,R5 | R_0805_2012Metric_Pad1.20x1.40mm_HandSolder | 2 | 1kOhm 5% ERJ-T06J102V | ERJ-T06J102V |  |  | 0,065 | 0,13
R11 | R_0805_2012Metric_Pad1.20x1.40mm_HandSolder | 1 | 22.1k 1% Würth WRIS-RSKS 560112120026 | 560112120026 |  |  | 0,13 | 0,13
R15 | R_0805_2012Metric_Pad1.20x1.40mm_HandSolder | 1 | 220 Ohm 5% ERJ-T06J221V | ERJ-T06J221V |  |  | 0,149 | 0,149
 |  |  |  |  |  |  |  | 0
 |  |  |  |  |  |  |  | 0
U4,U1,U3,U2 | PinSocket_1x08_P2.54mm_Vertical | 8 | 2,54mm pin socket BKL 10122206 8,5mm height | BKL 10122206 |  |  | 0,68 | 5,44
U4,U1,U3,U2 | MODULE_TMC2209_SILENTSTEPSTICK | 4 | TMC2209 |  |  |  |  | 0
 |  |  |  |  |  |  |  | 0
 |  |  |  |  |  |  |  | 0
J1 | 26011102 | 1 | WAGO 2601-1102 | WAGO 2601-1102 |  |  | 0,95 | 0,95
J2,J12,J10,J11,J9 | JST_XH_B2B-XH-A_1x02_P2.50mm_Vertical | 5 | JST XHP-2 | JST XHP-2 |  |  | 0,15 | 0,75
J13 | JST_XH_B3B-XH-A_1x03_P2.50mm_Vertical | 1 | JST XHP-3 | JST XHP-3 |  |  | 0,19 | 0,19
J19,J14 | JST_XH_B4B-XH-A_1x04_P2.50mm_Vertical | 2 | JST XHP-4 | JST XHP-4 |  |  | 0,23 | 0,46
J3 | JST_XH_B13B-XH-A_1x13_P2.50mm_Vertical | 1 | JST XHP-13 | JST XHP-13 |  |  | 1 | 1
J20 | PinHeader_1x02_P2.54mm_Vertical | 0 | Not used |  |  |  |  | 0
J15,J17,J7,J8 | TerminalBlock_Phoenix_MKDS-1,5-4_1x04_P5.00mm_Horizontal | 4 | 35° 4-pole screw terminal ( TE Connectivity 796689-4 ) | TE Connectivity 796689-4 |  |  | 1,73 | 6,92
J6 | PinSocket_1x19_P2.54mm_Vertical | 1 | 2,54mm pin socket 1x19 (1x20 cutted) BL 1X20G8 2,54 | BL 1X20G8 2,54 |  |  | 0,3 | 0,3
J5 | PinSocket_2x19_P2.54mm_Vertical | 1 | 2,54mm pin socket 2x19 (2x20 cutted) BKL 10120963 | BKL 10120963 |  |  | 1,55 | 1,55
JP3,JP5,JP4,JP6,JP2,JP7,JP1,JP8 | PinHeader_1x02_P2.54mm_Vertical | 8 | 1x02 pin header |  |  |  | 0,06 | 0,48
JP3,JP5,JP4,JP6,JP2,JP7,JP1,JP8 | Low profile jumper cap 2,54mm 4,5mm height | 8 | low profile jumper cap 4.5mm height 149-3-002-F0-XS | 149-3-002-F0-XS |  |  | 0,12 | 0,96
 |  |  |  |  |  |  |  | 0
 |  |  |  |  |  |  |  | 0
D3 | LED_0805_2012Metric_Pad1.15x1.40mm_HandSolder | 1 | 597-3305-607F | 597-3305-607F |  |  | 0,405 | 0,405
D1,D2 | D_SMA_Handsoldering | 2 | 60v3ASchottky B360A-E3/61T | B360A-E3/61T |  |  | 0,332 | 0,664
 |  |  |  |  |  |  |  | 0
 |  |  |  |  |  |  |  | 0
L1 | WE-PD_6033_6050_PLASTIC_BASE54 | 1 | SMD WE-PD 8.2uH 2.3A | WE-PD 7447786008 |  |  | 1,5 | 1,5
 |  |  |  |  |  |  |  | 0
 |  |  |  |  |  |  |  | 0
IC5 | SOT95P280X110-6N | 1 | SIMPLE SWITCHER power converter LMR51420XFDDCR | LMR51420XFDDCR |  |  | 1,31 | 1,31
IC3,IC4 | SOT95P240X110-3N | 2 | NPN transistor MMBT3904 | MMBT3904 |  |  | 0,06 | 0,12
IC1,IC2 | SOT254P916X480-6N | 2 | H11L1SR2M | H11L1SR2M |  |  | 0,939 | 1,878
 |  |  |  |  |  |  |  | 0
 |  |  |  |  |  |  |  | 0
 |  |  |  |  |  |  |  | 0
 |  |  |  |  |  |  |  | 0
 |  |  |  |  |  |  |  | 0
 |  |  |  |  |  |  |  | 0
 | AZ delivery 38Pin ESP32 NodeMCU WLAN Development Dev Kit C WiFi Bluetooth Board WROOM32 Espressif | 1 |  |  | 11,49 | Not icnluded |  | 0 | https://www.ebay.de/itm/144215008485
 | Silentstepstick TMC2209 | 4 |  |  | 10,62 | Not icnluded |  | 0
 |  |  |  |  |  |  |  | 0
 |  |  |  |  |  |  |  | 0
 |  |  |  |  |  |  |  | 0
 |  |  |  |  |  |  |  | 0
 |  |  |  |  |  |  |  | 0
 |  |  |  |  |  |  |  | 13,883

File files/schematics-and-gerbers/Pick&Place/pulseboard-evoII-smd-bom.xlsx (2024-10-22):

 | G-EDM Pulseboard EVOII – SMD/SMT BOM
Item # | *Designator | *Qty | Manufacturer | *Mfg Part # | Description / Value | *Package/Footprint | Type | Your Instructions / Notes
1 | C1,C6,C3,C10,C8 | 5 | KYOCERA AVX | 08055C104K4T2A | 0.1uf 50v X7R 10% MLCC | 0805 | SMD
2 | C29 | 1 | Murata Electronics | GRM32RR71H105KA01K | 1uf 50v X7R 10% MLCC | 1210 | SMD
3 | R13,R12,R6,R7 | 4 | YAGEO | RC2512JK-7W4R7L | 4.7 Ohm 2W 5% resistor | 2512 | SMD
4 | R9,R8,R15,R14 | 4 | KOA Speer | RK73B2ETTD104J | 100 kOhm 1/2W 5% resistor | 1210 | SMD
5 | R5 | 1 | Panasonic | ERJ-U12F1001U | 1 kOhm 3/4W 1% resistor | 1812 | SMD
6 | R42 | 1 | KOA Speer | RK73B2ATTD561J | 560 Ohm 1/4W 5% resistor | 0805 | SMD
7 | R2 | 1 | Würth | 560112120004 | 10 kOhm 1/4W 1% resistor | 0805 | SMD
8 | R1 | 1 | Würth | 560112120015 | 200 Ohm 1/4W 1% resistor | 0805 | SMD
9 | D6,D7,D3,D1,D19,D18 | 6 | Vishay General Semiconductor | B360A-E3/61T | 3A 60V Schottky diode | SMA (DO-214AC) | SMD
10 | D13 | 1 | Bivar | SM0805UGC | LED green 20mA 2v | 0805 | SMD
11 | IC5 | 1 | Lite-On | 6N137S | High Speed Optocoupler | PDIP-8-SMD | SMD

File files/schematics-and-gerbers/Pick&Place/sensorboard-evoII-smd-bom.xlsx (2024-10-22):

 | G-EDM Sensorboard EVOII – SMD/SMT BOM
Item # | *Designator | *Qty | Manufacturer | *Mfg Part # | Description / Value | *Package/Footprint | Type | Your Instructions / Notes
1 | C2,C13,C18,C20,C23,C27,C31,C32,C34,C36,C37,C40,C45,C46 | 14 | KYOCERA AVX | 08055C104K4T2A | 0.1uf 50v X7R 10% MLCC | 0805 | SMD
2 | C21,C22,C28,C35 | 4 | KEMET | C0805C101J5RACTU | 100pF 50v X7R 5% MLCC | 0805 | SMD
3 | R38,R39 | 2 | Vishay / Dale | RCC08050000Z0EA | Zero Ohm 1/4W resistor jumper | 0805 | SMD
4 | R32,R35 | 2 | Würth | 560112120015 | 200 Ohm 1/4W 1% resistor | 0805 | SMD
5 | R3,R41 | 2 | Panasonic | ERJ-T06J221V | 220 Ohm 1/4W 5% resistor | 0805 | SMD
6 | R26 | 1 | KOA Speer | RK73B2ATTD561J | 560 Ohm 1/4W 5% resistor | 0805 | SMD
7 | R20,R21,R25,R27 | 4 | Panasonic | ERJ-T06J102V | 1 kOhm 1/4W 5% resistor | 0805 | SMD
8 | R4,R30 | 2 | Vishay / Dale | RCC08054K70FKEA | 4.7 kOhm 1/4W 1% resistor | 0805 | SMD
9 | R10,R19,R22,R23,R24,R28 | 6 | Würth | 560112120004 | 10 kOhm 1/4W 1% resistor | 0805 | SMD
10 | R11,R17,R34,R37 | 4 | KOA Speer | RK73H2ARTTD2002F | 20 kOhm 1/4W 1% resistor | 0805 | SMD
11 | R16,R18,R29,R36 | 4 | Würth | 560112120013 | 100 kOhm 1/4W 1% resistor | 0805 | SMD
12 | IC1,IC2 | 2 | Texas Instruments | OPA350UA | High Speed rail-to-rail OpAmp single channel | SOIC-8 | SMD | Please validate the footprint
13 | IC6,IC9 | 2 | Texas Instruments | OPA2350UA | High Speed rail-to-rail OpAmp dual channel | SOIC-8 | SMD | Please validate the footprint
14 | IC8,IC3 | 2 | Broadcom / Avago | HCNR201-500E | High Linear Optocoupler | SOP-8 | SMD | Please validate the footprint
15 | IC4,IC7 | 2 | ROHM Semiconductor | LM358F-GE2 | Dual Grnd Sense Op Amp | SOP-8 | SMD | Please validate the footprint
16 | D5,D11 | 2 | Bivar | SM0805UGC | LED green 20mA 2v | 0805 | SMD
17 | D10 | 1 | Kingbright | APT2012LVBC/D | LED blue low current (starts to emit at 2mA) 2,65v | 0805 | SMD

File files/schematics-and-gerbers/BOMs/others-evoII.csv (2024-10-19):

Stückzahl | Bezeichnung | Price pre piece in Euro | Total | Datasheets
1 | Switching PSU, 12A 800W 65v (400W 70v could work too and cost only half) | 72,71 | 72,71 | https://www.ebay.de/itm/395514808705
1 | DPM8605 0-60v 0-5A 300W TTL/CMOS | 47,52 | 47,52 | https://www.ebay.de/itm/364243372630
1 | Switching PSU, 10A 120W 12v | 18,97 | 18,97 | https://www.ebay.de/itm/314155994709
1 | Amplifier DIY enclosure (this is a luxus box; Just needs to be an all metal box) | 109,99 | 109,99 | https://www.ebay.de/itm/254154113548
7 | Lapp ÖLFLEX CLASSIC 110 CY 4x0,75mm² shielded wire | 3 | 21 | https://www.ebay.de/itm/264470575385
5 | Lapp ÖLFLEX CLASSIC 110 CY 2x0,5mm² shielded wire | 3 | 15 | https://www.ebay.de/itm/275154935636
1 | DC connector female socket 5,5x2,5mm | 3,5 | 3,5 | https://www.ebay.de/itm/374396760936
1 | IEC socket | 5 | 5
1 | IEC (power) connector wire | 15 | 15
1 | ESP32 NodeMCU WROOM32 38 Pin Azdelivery | 11,49 | 11,49 | https://www.ebay.de/itm/144215008485
4 | Silentstepstick TMC2209 | 10,62 | 42,48
1 | PLA+ Filament 300g (300g is just a very rough number) | 10 | 10
1 | TPU Filament 200g (200g is just a very rough number) | 10 | 10
1 | Hailege 2.4" ILI9341 240x320 SPI TFT LCD Display Touch | 15,99 | 15,99
1 | On/Off switch | 1 | 1 | https://www.amazon.de/Wippschalter-2-polig-KCD1-Schalter-Haushaltsger%C3%A4te-Schwarz
1 | Different JST wires.. 2pole, 13pole, 3 pole 4 pole | 25 | 25
1 | 40mm fan (I use 24v running it at 12v for silence) | 5 | 5
1 | 120mm fan artic P12 silent 3pole | 10 | 10
 |  |  | 439,65
 | Note: Cheap fans can introduce more noise in the system.
 | Also high speed fans are also not recommended.
 | The prices are ebay/amazon prices and it should be no problem to get it down a little

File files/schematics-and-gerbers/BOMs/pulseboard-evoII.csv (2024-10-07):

Bezeichner | Footprint | Stückzahl | Bezeichnung | Anbieter und Referenz |  | Price in Euro per piece | Total Euro | Datasheets
C5 | C_1206_3216Metric_Pad1.33x1.80mm_HandSolder | 1 | 47pf50v 08055C470KAT2A | Not used
C29 | C_1210_3225Metric_Pad1.33x2.70mm_HandSolder | 1 | 1uf50v GRM32RR71H105KA01K | GRM32RR71H105KA01K |  | 0,595 | 0,595
C1,C6,C3,C10,C8 | C_0805_2012Metric_Pad1.18x1.45mm_HandSolder | 5 | 0.1uf-50v-x7r 08055C104K4T2A | 08055C104K4T2A |  | 0,043 | 0,215
 |  |  |  |  |  |  | 0
C14,C11,C9 | C_Disc_D5.0mm_W2.5mm_P5.00mm | 3 | C100pf500v KERKO-500 100P | KERKO-500 100P |  | 0,04 | 0,12
C7 | CP_Radial_D6.3mm_P2.50mm | 1 | 220uf16v RD1C227M6L011M18 | RD1C227M6L011M18 |  | 0,06 | 0,06
C4 | CP_Radial_D14.0mm_P5.00mm | 1 | CAMION Photo Flash 100µF 330V | Not used with the DPM |  |  | 0
C15 | CP_Radial_D8.0mm_P3.50mm | 1 | 220uf35v RD1V227M0811M160 | RD1V227M0811M160 |  | 0,09 | 0,09
C19 | CP_Radial_D10.0mm_P5.00mm | 1 | 470uf35v RD1V477M10016100 | RD1V477M10016100 |  | 0,2 | 0,2
 |  |  |  |  |  |  | 0
 |  |  |  |  |  |  | 0
R13,R12,R6,R7 | R_2512_6332Metric_Pad1.40x3.35mm_HandSolder | 4 | 4.7Ohm RC2512JK-7W4R7L | RC2512JK-7W4R7L |  | 0,184 | 0,736
R9,R8,R15,R14 | R_1210_3225Metric | 4 | 100k RK73B2ETTD104J | RK73B2ETTD104J |  | 0,052 | 0,208
R5 | R_1812_4532Metric_Pad1.30x3.40mm_HandSolder | 1 | 1% 1.0Kohm ERJ-U12F1001U | ERJ-U12F1001U |  | 0,217 | 0,217
R42 | R_0805_2012Metric_Pad1.20x1.40mm_HandSolder | 1 | 560Ohm RK73B2ATTD561J | RK73B2ATTD561J |  | 0,015 | 0,015
R2 | R_0805_2012Metric_Pad1.20x1.40mm_HandSolder | 1 | 10kOhm WRIS-RSKS 560112120004 | 560112120004 |  | 0,073 | 0,073
R1 | R_0805_2012Metric_Pad1.20x1.40mm_HandSolder | 1 | 200Ohm WRIS-RSKS 560112120015 | 560112120015 |  | 0,073 | 0,073
 |  |  |  |  |  |  | 0
R33 | R_Axial_DIN0411_L9.9mm_D3.6mm_P5.08mm_Vertical | 1 | 4.7kOhm 2W CPF24K7000BHB14 | CPF24K7000BHB14 |  | 1,7 | 1,7
R31 | R_Axial_DIN0414_L11.9mm_D4.5mm_P5.08mm_Vertical | 1 | 0Ohm (bridged) | Leg of a big diode |  |  | 0
 |  |  |  |  |  |  | 0
 |  |  |  |  |  |  | 0
J17,J19 | DEGSONDG135T101602P1300AH | 2 | Degson DG135T-10.16-02P-13-00AH | DG135T-10.16-02P-13-00AH |  | 1,55 | 3,1
J4,J7,J2,J8,J15 | JST_XH_S2B-XH-A_1x02_P2.50mm_Horizontal | 5 | JST_XH_S2B-XH-A_1x02_P2.50mm_Horizontal | JST_XH_S2B-XH-A_1x02 |  | 0,23 | 1,15
J6 | plug terminal 2 pole 5mm grid female | 1 | 1 | TE Connectivity 1776138-2 | 1776138-2 | 0,67 | 0,67
J6 | plug terminal 2 pole 5mm grid male | 1 | 1 | TE Connectivity 796641-2 | 796641-2 | 1 | 1
 |  |  |  |  |  |  | 0
 |  |  |  |  |  |  | 0
D20, D21 | D_DO-201_P5.08mm_Vertical_AnodeUp | 1 | 200V 5A Schottky SR520 | SR520 |  | 0,2 | 0,2
D6,D7,D3,D1,D19,D18 | D_SMA_Handsoldering | 6 | 60v3ASchottky B360A-E3/61T | B360A-E3/61T |  | 0,332 | 1,992
D14,D15 | D_DO-201_P5.08mm_Vertical_AnodeUp | 2 | 1N5379B 110v Zener | 1N5379B |  | 0,304 | 0,608
 |  |  |  |  |  |  | 0
 |  |  |  |  |  |  | 0
U2 | TO255P460X1020X2008-3P | 1 | voltage regulator 5v 1.5A L7805CV | L7805CV |  | 0,539 | 0,539
 |  |  |  |  |  |  | 0
 |  |  |  |  |  |  | 0
Q3,Q2,Q4,Q1 | TO-247-3_Horizontal_TabUp | 4 | IRFP260NPBF | IRFP260NPBF |  | 2,65 | 10,6
Q8 | TO-3PB-3_Vertical | 1 | 2SB688 | 2SB688 |  | 1,2 | 1,2
Q7,Q10 | TO-3PB-3_Vertical | 2 | 2SD718 | 2SD718 |  | 1,2 | 2,4
 |  |  |  |  |  |  | 0
 |  |  |  |  |  |  | 0
D13 | LED_0805_2012Metric_Pad1.15x1.40mm_HandSolder | 1 | SM0805UGC | SM0805UGC |  | 0,357 | 0,357
D17 | D_SMC_Handsoldering | 1 | TVS Diode 3kw | Not used |  |  | 0
 |  |  |  |  |  |  | 0
 |  |  |  |  |  |  | 0
VR1 | 3006P1103 | 1 | 3006P-1-103 10k Trimpoti | 3006P-1-103 |  | 1,35 | 1,35
 |  |  |  |  |  |  | 0
 |  |  |  |  |  |  | 0
IC5 | SOP254P1016X460-8N | 1 | 6N137S | 6N137S |  | 0,791 | 0,791
 |  |  |  |  |  |  | 0
 |  |  |  |  |  |  | 0
 |  |  |  |  |  |  | 0
 |  |  |  |  |  |  | 0
 |  |  |  |  |  |  | 0
 |  |  |  |  |  |  | 0
U2 | Small heatsink (not needed) | 1 | TO220 Aluminum heatsink set 15x20 |  |  | 1 | 1 | https://www.ebay.de/itm/126202543117
Q3,Q2,Q4,Q1 | Heatsink for mosfets | 1 | Fischer Elektronik 10020621 SK 48 100 SA | SK 48 100 SA |  | 7,49 | 7,49
Q3,Q2,Q4,Q1 | IB 16 Insulating bushing | 4 | Fischer Elektronik IB 16 | IB 16 |  | 0,13 | 0,52 | https://cdn-reichelt.de/documents/datenblatt/C800/FISCHERELEKTRONIK_IB_16.pdf
Q3,Q2,Q4,Q1 | Insulating film for mosfet/heatsink connection | 1 | SI6018 Silicone insulating film 94x20x0,18mm | SI6018 |  | 1,99 | 1,99 | https://cdn-reichelt.de/documents/datenblatt/C800/SI6018%23ALU.pdf
 |  |  |  |  |  | 26,325 | 41,259

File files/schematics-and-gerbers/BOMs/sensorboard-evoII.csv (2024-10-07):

Bezeichner | Footprint | Stückzahl | Bezeichnung | Anbieter und Referenz |  | Price per piece in Euros | Total
C17,C30 | C_0805_2012Metric_Pad1.18x1.45mm_HandSolder | 2 | 47pf not used | not used
C21,C22,C28,C35 | C_0805_2012Metric_Pad1.18x1.45mm_HandSolder | 4 | 100pf50v X7R C0805C101J5RACTU | C0805C101J5RACTU |  | 0,055 | 0,22
C2,C13,C18,C20,C23,C27,C31,C32,C34,C36,C37,C40,C45,C46 | C_0805_2012Metric_Pad1.18x1.45mm_HandSolder | 14 | 0.1uf-50v-x7r 08055C104K4T2A | 08055C104K4T2A |  | 0,053 | 0,742
 |  |  |  |  |  |  | 0
C24 | C_Disc_D5.1mm_W3.2mm_P5.00mm | 1 | C100pf500v KERKO-500 100P | KERKO-500 100P |  | 0,04 | 0,04
C16,C39,C41,C44 | CP_Radial_D5.0mm_P2.50mm | 4 | 47uf63v RD1J476M6L011M18 | RD1J476M6L011M18 |  | 0,05 | 0,2
C26 | CP_Radial_D8.0mm_P3.50mm | 1 | 220uf35v RD1V227M0811M160 | RD1V227M0811M160 |  | 0,09 | 0,09
C12,C25 | CP_Radial_D10.0mm_P5.00mm | 2 | 220uf50v RD1H227M1012M128 | RD1H227M1012M128 |  | 0,2 | 0,4
C33,C38,C42,C43 | CP_Radial_D5.0mm_P2.50mm | 4 | X not used | not used |  |  | 0
 |  |  |  |  |  |  | 0
 |  |  |  |  |  |  | 0
R38,R39 | R_0805_2012Metric_Pad1.20x1.40mm_HandSolder | 2 | Zero Ohm RCC08050000Z0EA | RCC08050000Z0EA |  | 0,039 | 0,078
R32,R35 | R_0805_2012Metric_Pad1.20x1.40mm_HandSolder | 2 | 200Ohm WRIS-RSKS 560112120015 | 560112120015 |  | 0,073 | 0,146
R3,R41 | R_0805_2012Metric_Pad1.20x1.40mm_HandSolder | 1 | 220 Ohm 5% ERJ-T06J221V | ERJ-T06J221V |  | 0,149 | 0,149
R26 | R_0805_2012Metric_Pad1.20x1.40mm_HandSolder | 1 | 560Ohm RK73B2ATTD561J | RK73B2ATTD561J |  | 0,015 | 0,015
R20,R21,R25,R27 | R_0805_2012Metric_Pad1.20x1.40mm_HandSolder | 4 | 1kOhm 5% ERJ-T06J102V (better 1%) | ERJ-T06J102V |  | 0,065 | 0,26
R4,R30 | R_0805_2012Metric_Pad1.20x1.40mm_HandSolder | 2 | 4k7 1% RCC08054K70FKEA | RCC08054K70FKEA |  | 0,043 | 0,086
R10,R19,R22,R23,R24,R28 | R_0805_2012Metric_Pad1.20x1.40mm_HandSolder | 6 | 10k 1% WRIS-RSKS 560112120004 | 560112120004 |  | 0,13 | 0,78
R11,R17,R34,R37 | R_0805_2012Metric_Pad1.20x1.40mm_HandSolder | 4 | 20k 1% RK73H2ARTTD2002F | RK73H2ARTTD2002F |  | 0,146 | 0,584
R16,R18,R29,R36 | R_0805_2012Metric_Pad1.20x1.40mm_HandSolder | 4 | 100k 1% Würth WRIS-RSKS 560112120013 | 560112120013 |  | 0,13 | 0,52
R40,R43 | R_0805_2012Metric_Pad1.20x1.40mm_HandSolder | 2 | not used | not used |  |  | 0
 |  |  |  |  |  |  | 0
R44 | R_Axial_DIN0414_L11.9mm_D4.5mm_P5.08mm_Vertical | 1 | 1kOhm 1W MBE04140C1001FC100 | MBE04140C1001FC100 |  | 0,289 | 0,289
 |  |  |  |  |  |  | 0
 |  |  |  |  |  |  | 0
RV4,RV2,RV1,RV3 | Potentiometer_Bourns_3296W_Vertical | 4 | 3296W Poti 10kOhm 3296W-1-103LF | 3296W-1-103LF |  | 2,17 | 8,68
 |  |  |  |  |  |  | 0
 |  |  |  |  |  |  | 0
J1,J9,J10,J11 | JST_XH_S2B-XH-A_1x02_P2.50mm_Horizontal | 4 | JST_XH_S2B-XH-A_1x02_P2.50mm_Horizontal | JST_XH_S2B-XH-A |  | 0,23 | 0,92
J3 | JST_XH_S3B-XH-A_1x03_P2.50mm_Horizontal | 1 | JST_XH_S3B-XH-A_1x03_P2.50mm_Horizontal | JST_XH_S3B-XH-A |  | 0,28 | 0,28
J14,J13 | JST_XH_B2B-XH-A_1x02_P2.50mm_Vertical | 2 | JST XHP-2 | JST XHP-2 |  | 0,15 | 0,3
J5 | TE connectivity 2 pole terminal 5mm grid | 1 | female | 1776138-2 | 1776138-2 | 0,67 | 0,67
J5 | TE connectivity 2 pole terminal 5mm grid | 1 | male | 796641-2 | 796641-2 | 1 | 1
 |  |  |  |  |  |  | 0
 |  |  |  |  |  |  | 0
IC1,IC2 | SOIC127P600X175-8N | 2 | OPA350UA single channel OpAmp | OPA350UA |  | 2,59 | 5,18
IC6,IC9 | SOP-8_3.9x4.9mm_P1.27mm | 2 | OPA2350UA dual channel OpAmp | OPA2350UA |  | 4,1 | 8,2
IC8,IC3 | SOP254P1230X400-8N | 2 | HCNR201-500E | HCNR201-500E |  | 5,48 | 10,96
IC4,IC7 | SOP-8_3.9x4.9mm_P1.27mm | 2 | LM358F-GE2 | LM358F-GE2 |  | 0,495 | 0,99
J12 | DIP-6_W7.62mm_LongPads | 1 | PCB3007-1 Adapter | PCB3007-1 |  | 2,4 | 2,4
J12 | PCB3007-1 Adapter | 1 | INA293B3QDBVRQ1 current sensor ic | INA293B3QDBVRQ1 |  | 3,23 | 3,23
 |  |  |  |  |  |  | 0
 |  |  |  |  |  |  | 0
JP3 | PinHeader_1x02_P2.54mm_Vertical | 1 | 1x02 pin header (not used) |  |  |  | 0
JP1 | PinHeader_1x02_P2.54mm_Vertical | 1 | 1x02 pin header |  |  | 0,06 | 0,06
JP1 | jumper cap | 1 | jumper cap 149-3-002-F0-XS | 149-3-002-F0-XS |  | 0,12 | 0,12
 |  |  |  |  |  |  | 0
 |  |  |  |  |  |  | 0
D2 | D_DO-41_SOD81_P3.81mm_Vertical_AnodeUp | 1 | 5.1v Zener (Not used) | not used |  |  | 0
D9,D8 | D_DO-201_P5.08mm_Vertical_AnodeUp | 2 | 1N5379B 100v or 110v Zener | 1N5379B |  | 0,304 | 0,608
D5,D11 | LED_0805_2012Metric_Pad1.15x1.40mm_HandSolder | 2 | SM0805UGC | SM0805UGC |  | 0,357 | 0,714
D10 | LED_0805_2012Metric_Pad1.15x1.40mm_HandSolder | 1 | APT2012LVBC/D | APT2012LVBC/D |  | 0,368 | 0,368
 |  |  |  |  |  |  | 0
 |  |  |  |  |  |  | 0
PS1 | RS3K2405SZH3 | 1 | RS3K-2405SZ/H3 isolated DC/DC converter 5v | RS3K-2405SZ/H3 |  | 7,89 | 7,89
 |  |  |  |  |  |  | 0
 |  |  |  |  |  |  | 0
 |  |  |  |  |  |  | 0
 |  |  |  |  |  |  | 0
 |  |  |  |  |  |  | 0
 |  |  |  |  |  |  | 0
 |  |  |  |  |  |  | 0
 |  |  |  |  |  |  | 57,169

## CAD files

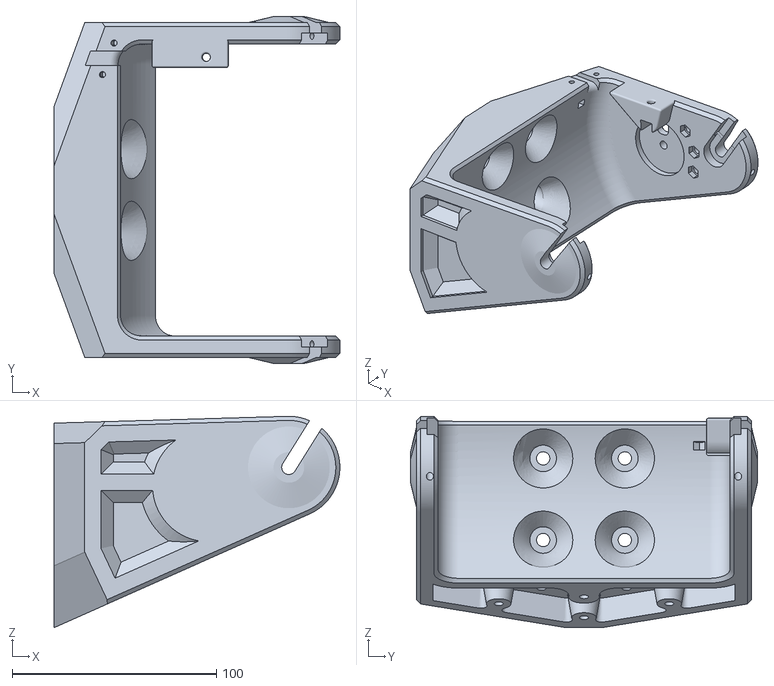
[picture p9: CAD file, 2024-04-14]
files/spool-holder/spool-holder-main.stl
140.0 x 170.0 x 103.5

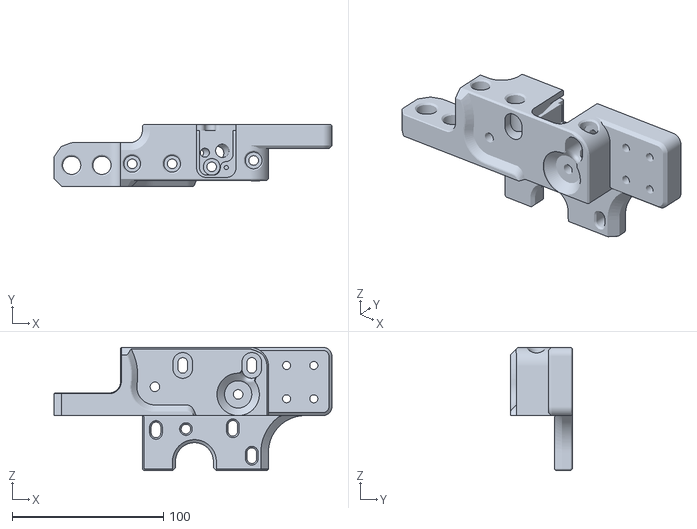
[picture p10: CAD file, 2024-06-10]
files/wire-extension-evo/wire-extension-main-connector.stl
183.7 x 41.0 x 81.5

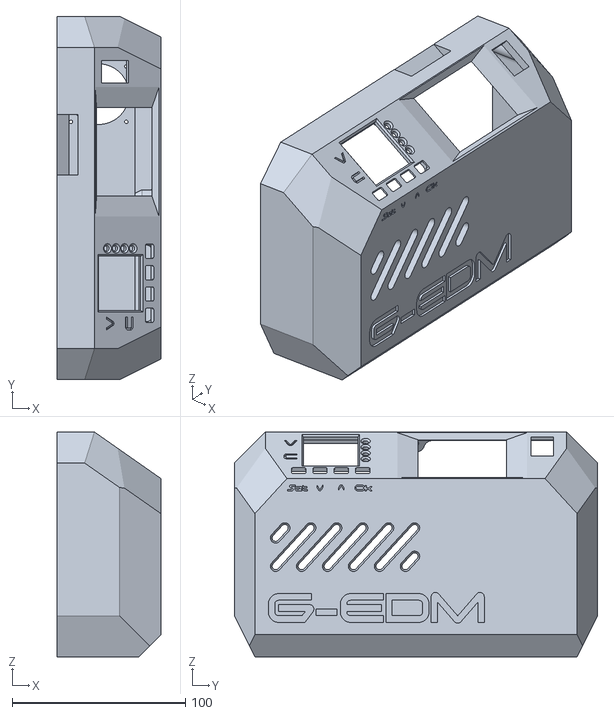
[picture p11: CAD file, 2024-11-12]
files/controlpanel-evo2/stl/EVOII-panel-ref2.stl
60.0 x 210.0 x 130.0

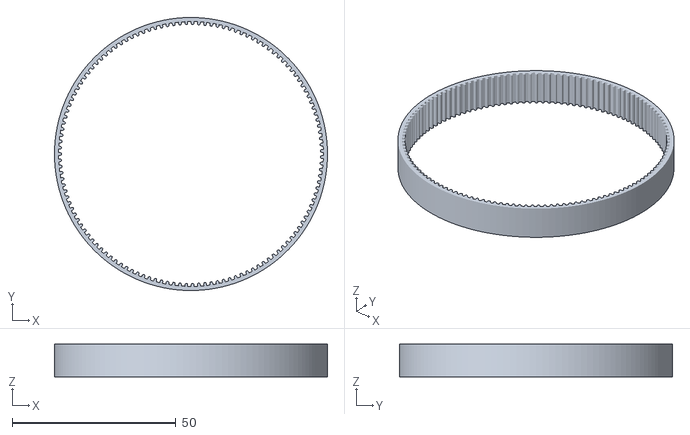
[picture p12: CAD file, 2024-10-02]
files/EVO2-ROUTER/belts-pulleys/belt-gt2-131T-262mm-10mm.stl
83.4 x 83.4 x 10.0

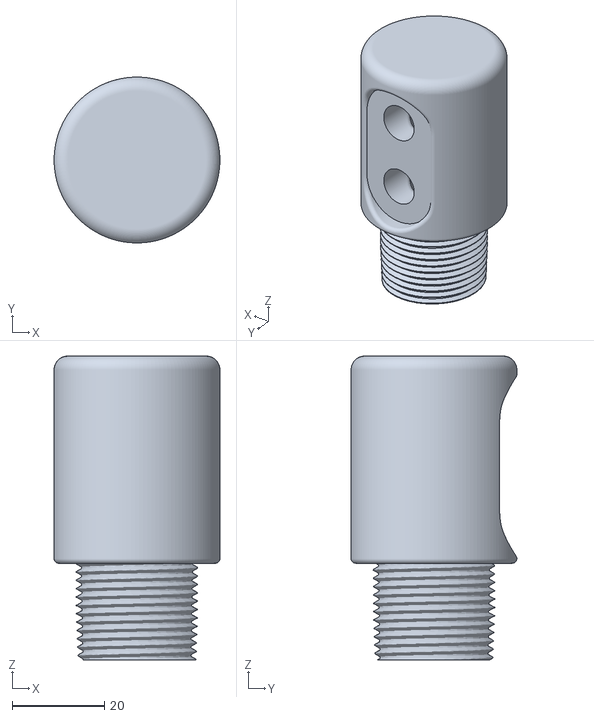
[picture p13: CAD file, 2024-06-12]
files/EVO2-ROUTER/misc/water-flow-nozzle-dual-hose-34.stl
36.0 x 36.0 x 66.0

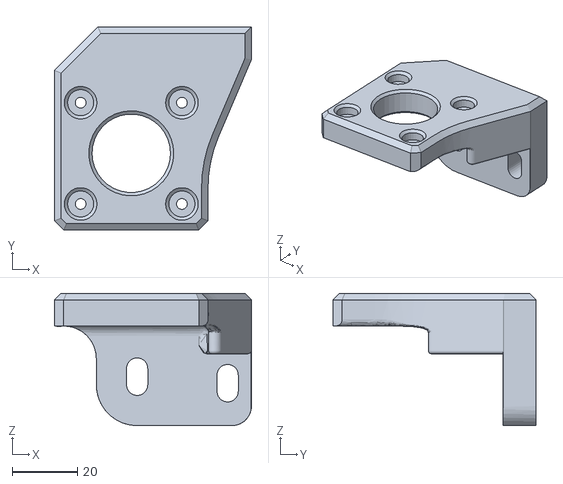
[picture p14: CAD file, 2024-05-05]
files/EVO2-ROUTER/temporary-hacks/rewinder-spool-motor-bracket-v2.stl
60.3 x 62.2 x 40.5

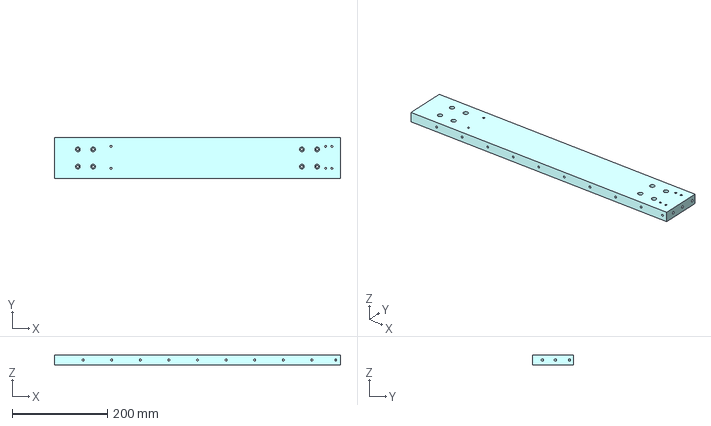
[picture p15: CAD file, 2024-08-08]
files/EVO2-ROUTER/x-axis/portal-plate-freecad-project.FCStd
600.0 x 85.0 x 20.0 mm

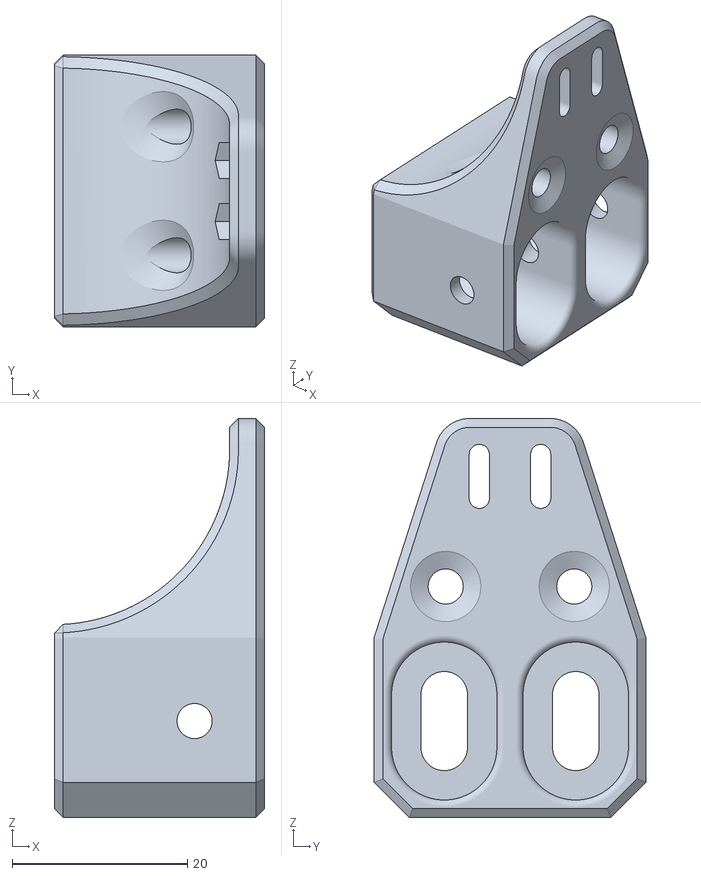
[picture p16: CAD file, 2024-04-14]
files/EVO2-ROUTER/y-axis/y-limit-switch-bracket.stl
24.0 x 31.0 x 45.5

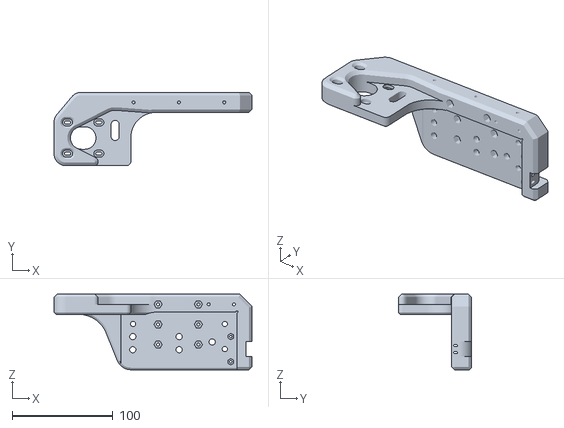
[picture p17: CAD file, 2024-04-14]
files/EVO2-ROUTER/z-axis/z-axis-motor-bracket.stl
196.5 x 72.9 x 75.0

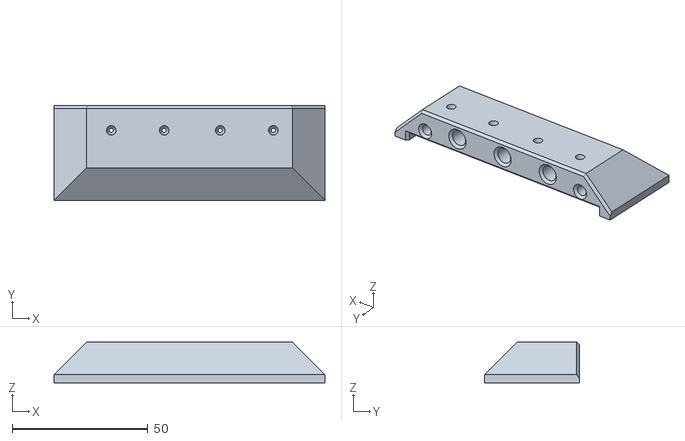
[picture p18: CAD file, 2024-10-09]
files/useful/evo-cube-75mmx88mm-heatsink-drill-jig.stl
100.0 x 35.0 x 15.0

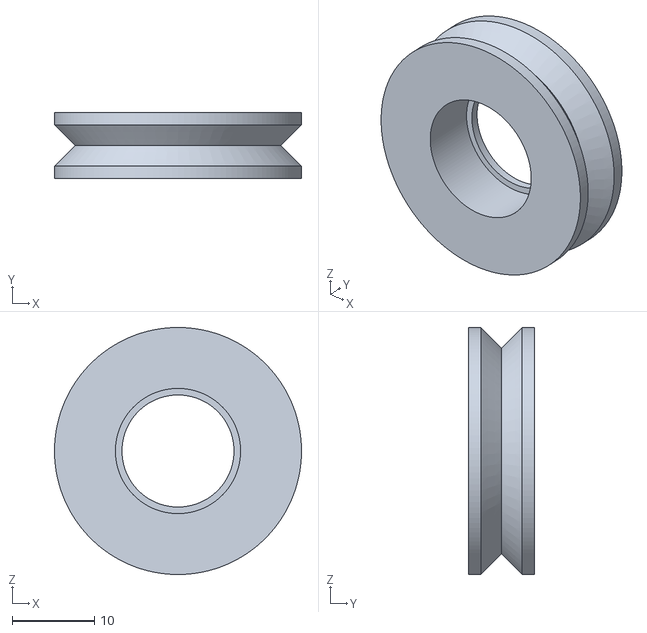
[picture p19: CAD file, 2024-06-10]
files/wire-extension-evo/temporary-hacks/15x6x5bearing-to-30mm-vgroove.stl
30.0 x 8.00 x 30.0

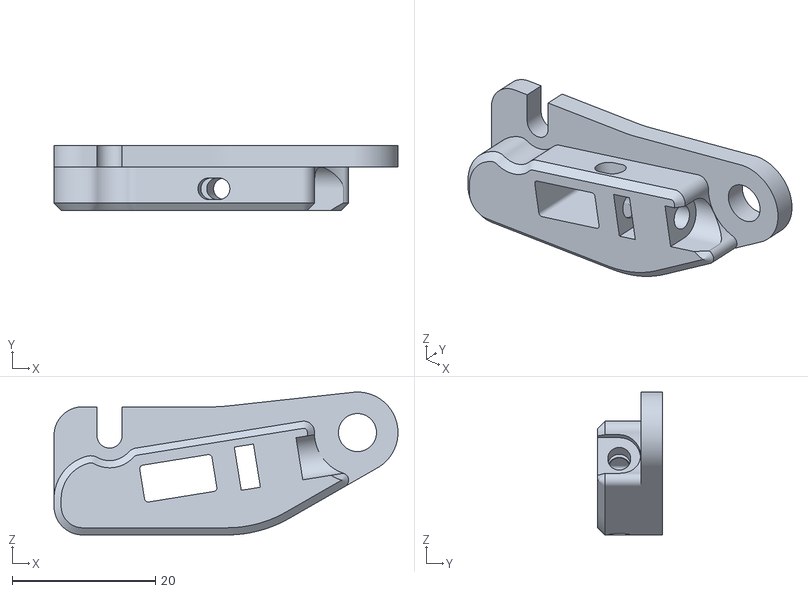
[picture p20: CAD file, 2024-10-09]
files/wire-extension-evo/tmp-current-contact-mount-v2.stl
48.0 x 9.00 x 19.9

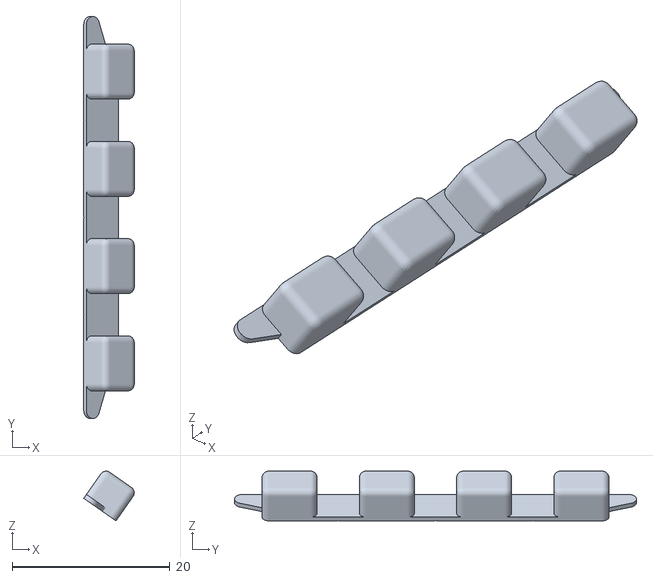
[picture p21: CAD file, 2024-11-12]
files/controlpanel-evo2/stl/EVOII-panel-ref2-DPM-buttons.stl
6.42 x 51.0 x 6.32

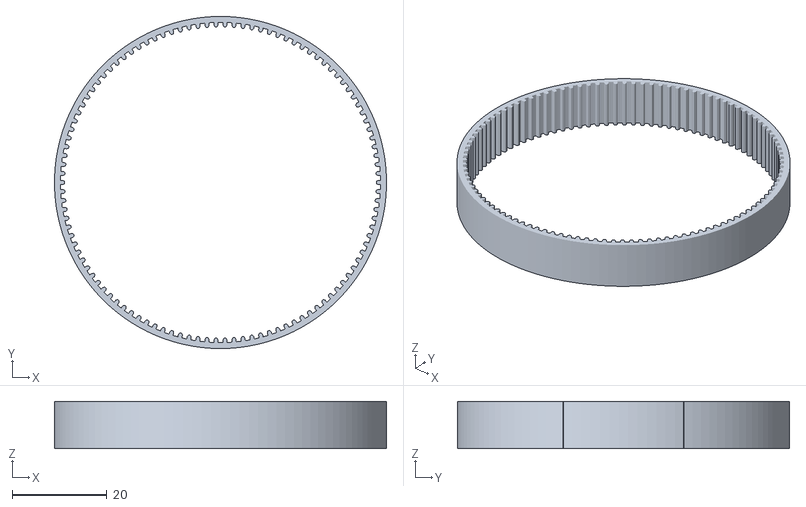
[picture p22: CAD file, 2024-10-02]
files/EVO2-ROUTER/belts-pulleys/GT2-Belt-220mm-110T-10mm.stl
70.0 x 70.1 x 10.0

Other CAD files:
files/EVO2-ROUTER/misc/water-flow-nozzle-half-inch.stl
files/EVO2-ROUTER/temporary-hacks/wire-mount-adapter-v4.stl
files/EVO2-ROUTER/x-axis/portal-plate.step
files/EVO2-ROUTER/y-axis/BF12-support-bracket.stl
files/EVO2-ROUTER/belts-pulleys/GT2-Belt-224mm-112T-10mm.stl
files/EVO2-ROUTER/belts-pulleys/Pulley_GT2_20T_5mmBore_10mm_belt.stl
files/EVO2-ROUTER/belts-pulleys/Pulley_GT2_60T_10mmBore_10mm_belt.stl
files/EVO2-ROUTER/belts-pulleys/belt-gt2-130T-260mm-10mm.stl
files/EVO2-ROUTER/belts-pulleys/belt-gt2-132T-264mm-10mm.stl
files/EVO2-ROUTER/belts-pulleys/belt-gt2-133T-266mm-10mm.stl
files/EVO2-ROUTER/belts-pulleys/unused/GT2-Belt-230mm-115T-10mm.stl
files/EVO2-ROUTER/belts-pulleys/unused/GT2-Belt-240mm-120T-too-long.stl
files/EVO2-ROUTER/belts-pulleys/unused/GT2-closed-TPU-belt-116T-232mm.stl
files/EVO2-ROUTER/belts-pulleys/unused/belt-gt2-135T-270mm-10mm.stl
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

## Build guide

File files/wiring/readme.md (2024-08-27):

The sensorboard and the pulseboard are connected with 3 JST connectors.

The connectors are placed at the exact same position. Don't use the wrong connector!
I shared a few images in the past where the PWM from the sensorboard was connected to the 5v output on the
pulseboard. It will burn the ESP32.

Sensorboard => Pulseboard

J10 => J8
J11 => J2
J9  => J7

Before connecting J9 to J7 make sure the voltage on J7 is below 5v! This is important. Use the Poti on the pulseboard to adjust it while
the PSU is ON. The output of J7 should remain a little below 5v at the max voltage provided from the DPM.

If a higher voltage is used adjust the Poti again. 
If 80v is used the output should be 4.8v while the big terminal is at 80v.
If 60v is used the output should be 4.8v while the big terminal is at 60v.

The board has 100v Zener diodes. Up to 90v should be ok.

The sensorboard provides 3.3v output and isolated 5v output. It is not used for anything yet.
The pulseboard provides 5v output that is also not used.

The pulseboard also provides a 12v output to connect a fan but it is not tested. Cheap high speed fans may introduce noise. There are flyback diodes
but if used connect a larger slow fan like a 120mm arctic fan.

# DPM to pulseboard

Connect the DPM8605 negative to the left side of the left big terminal (J19) and the positive to the right side of the same terminal.

The left side of the right terminal (J17) is bridged to the left terminals positive. The Shunt and wire is always hot and only GND is switched.
Connect the left side of J17 to one side of the shunt and the other side is the spark positive output.
The spark negative goes back into the right side of J17.

# Shunt to sensorboard
Connect both sides of the shunt to the sensorboard J5. It is no problem to wire it wrong here. If connected wrong it will not provide a feedback but will not destroy anything. Just swap the wire if there is no feedback.

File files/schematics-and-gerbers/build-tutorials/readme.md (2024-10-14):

# Not finished yet

The folder contains a step by step image slide show.

It will be separated into SMD top/bottom sides and Through Hole components for top/bottom sides of the PCBs.

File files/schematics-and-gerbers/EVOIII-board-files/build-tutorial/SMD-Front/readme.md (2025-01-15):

Warning:
The Pin 1 marking on the optocoupler 6N137S is wrong. 
Don't have time to change the image yet but the dot points in the other direction 
to where the Pin1 marking line is on the PCB.

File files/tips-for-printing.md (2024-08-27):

To print the big parts wihout warping it is necessary to add some adhesive to the printbed and change the support settings to get a stronger bond between model and supports. Another thing that is highly recommended is to add some kind of dust wiper to the filament. 

The print may take long and a few dust particle can lead to a clogged nozzle. A simple DIY dust wiper can be made with a zip tie and a piece of old lint free cloth. I have two dust wipers on the filament. Both are hook and loop fasteners wrapped around the filament with the fluffy part on the inside. Neoprene works too. A dust wiper can be the main problem solver on very long prints.

As adhesive I use a thick layer of strong hairspray on an ender 3v2 bed. Works very well but may not work at all on some specific printbeds used on other printers. Don't know what adhesive should be used on flexible beds.

It is also needed to add a brim. The default brim I use is 20mm. This is not possible for all parts. It is possible to use a smaller brim and then use cura patches on critical edges.

Another thing are the supports. After reinstalling my OS with a fresh cura install the supports stopped touching the print and even small chamfers on smaller parts started warping. This can be fixed in the cura settings.

Support Z Distance
Support X/Y Distance

Reducing this values will bring the support closer to the model.

Usinf 0.2mm for both of those settings will provide a strong fuse between support and model. This is good for the big parts. Note that the supports are hard to remove and this settings will only work for the big parts to prevent warping.

The big parts are printed with supports touching build plate. So it is Ok to have the supports fused to the model.

Also enable support interface. This will generate a support roof that help with fusing.

Support Distance Priority set to Z overrides X/Y. This is also necessary. With the Z axis moving up the XY distancae of the support will get smaller-

Thanks to 3dprinterly for his nice explaination:
https://3dprinterly.com/how-to-fix-cura-supports-not-touching-model-or-print/

Best way is to create a custom print profile for the heavy prints and use another for the normal prints where we want to easily remove the supports and don't have big risk of warping.

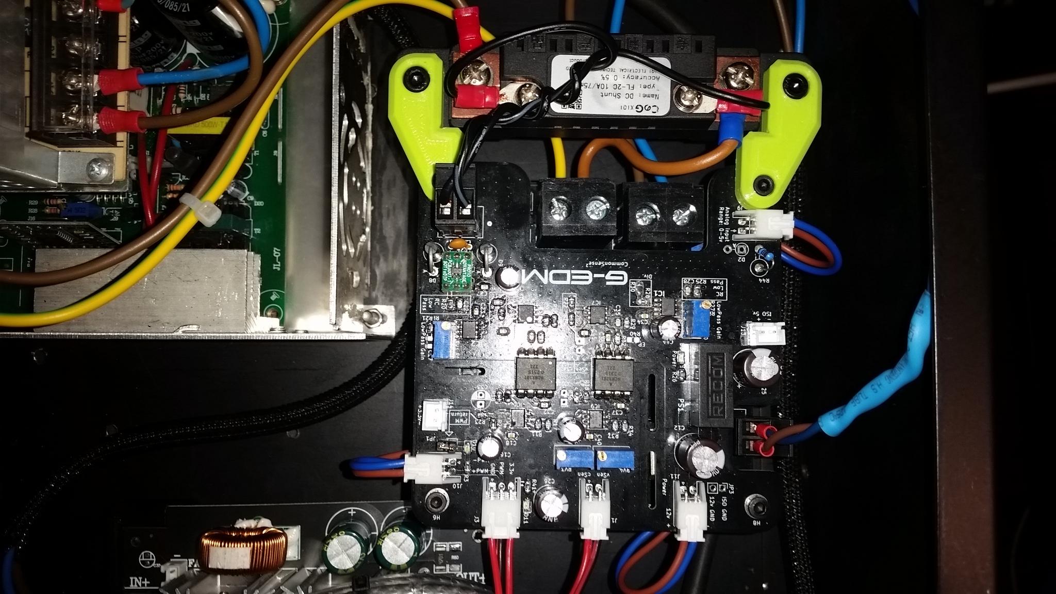
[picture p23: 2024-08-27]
files/wiring/images/20240827_085047.jpg

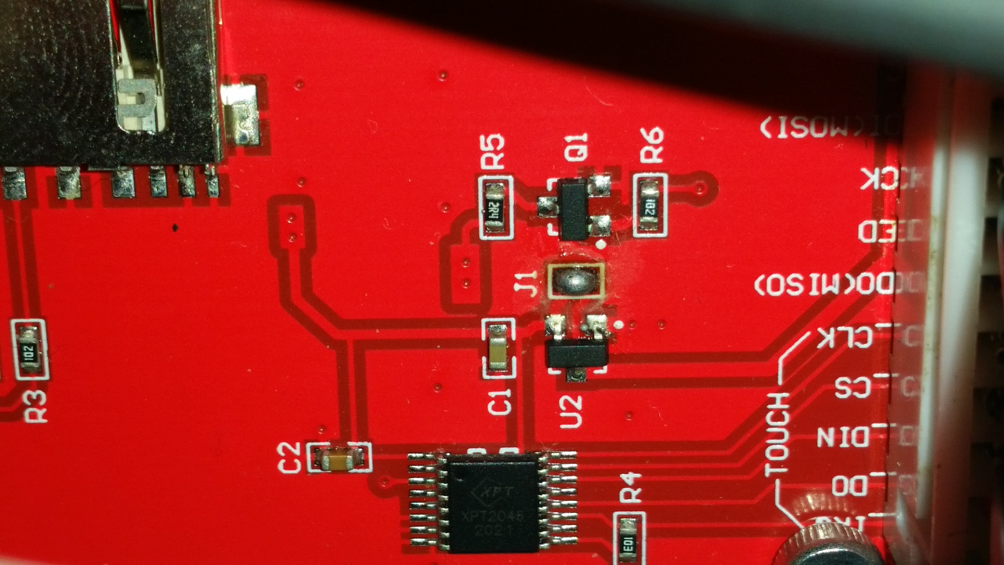
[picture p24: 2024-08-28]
files/wiring/images/20240828_004042.jpg

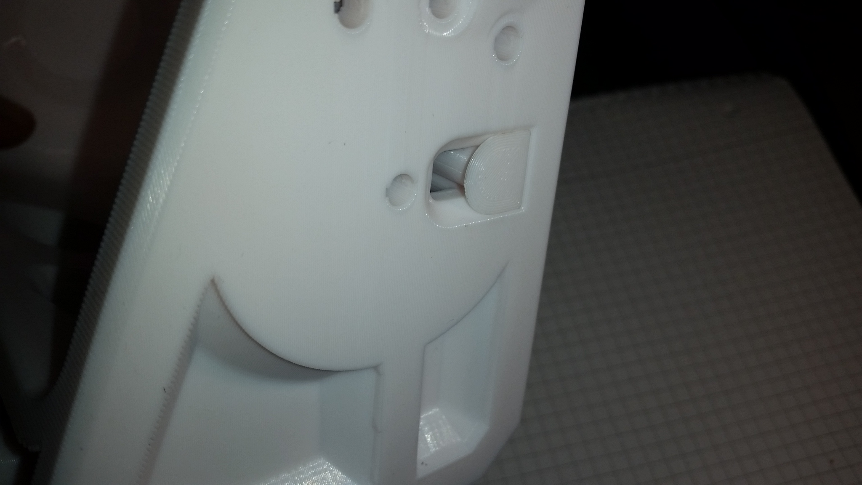
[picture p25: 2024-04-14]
files/spool-holder/images/build-tutorial-images/7b.jpg

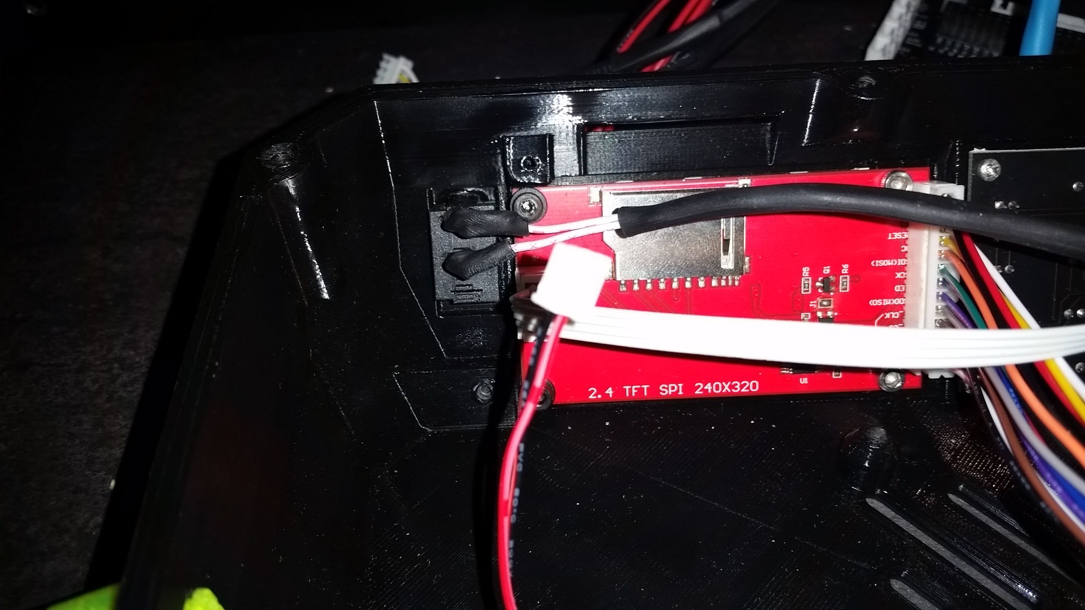
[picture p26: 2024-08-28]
files/wiring/images/20240828_004132.jpg

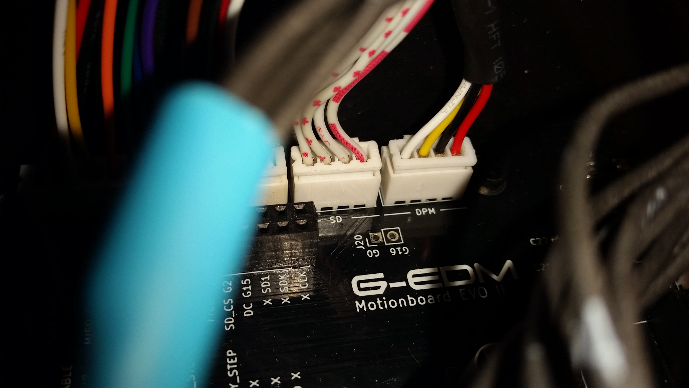
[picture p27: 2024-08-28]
files/wiring/images/20240828_010326.jpg

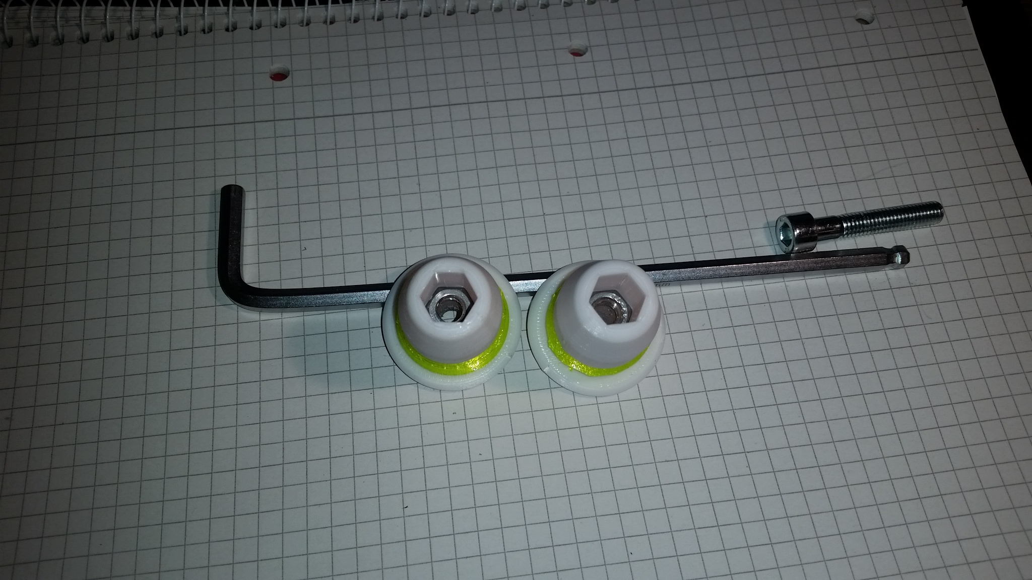
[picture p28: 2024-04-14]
files/spool-holder/images/build-tutorial-images/2.jpg

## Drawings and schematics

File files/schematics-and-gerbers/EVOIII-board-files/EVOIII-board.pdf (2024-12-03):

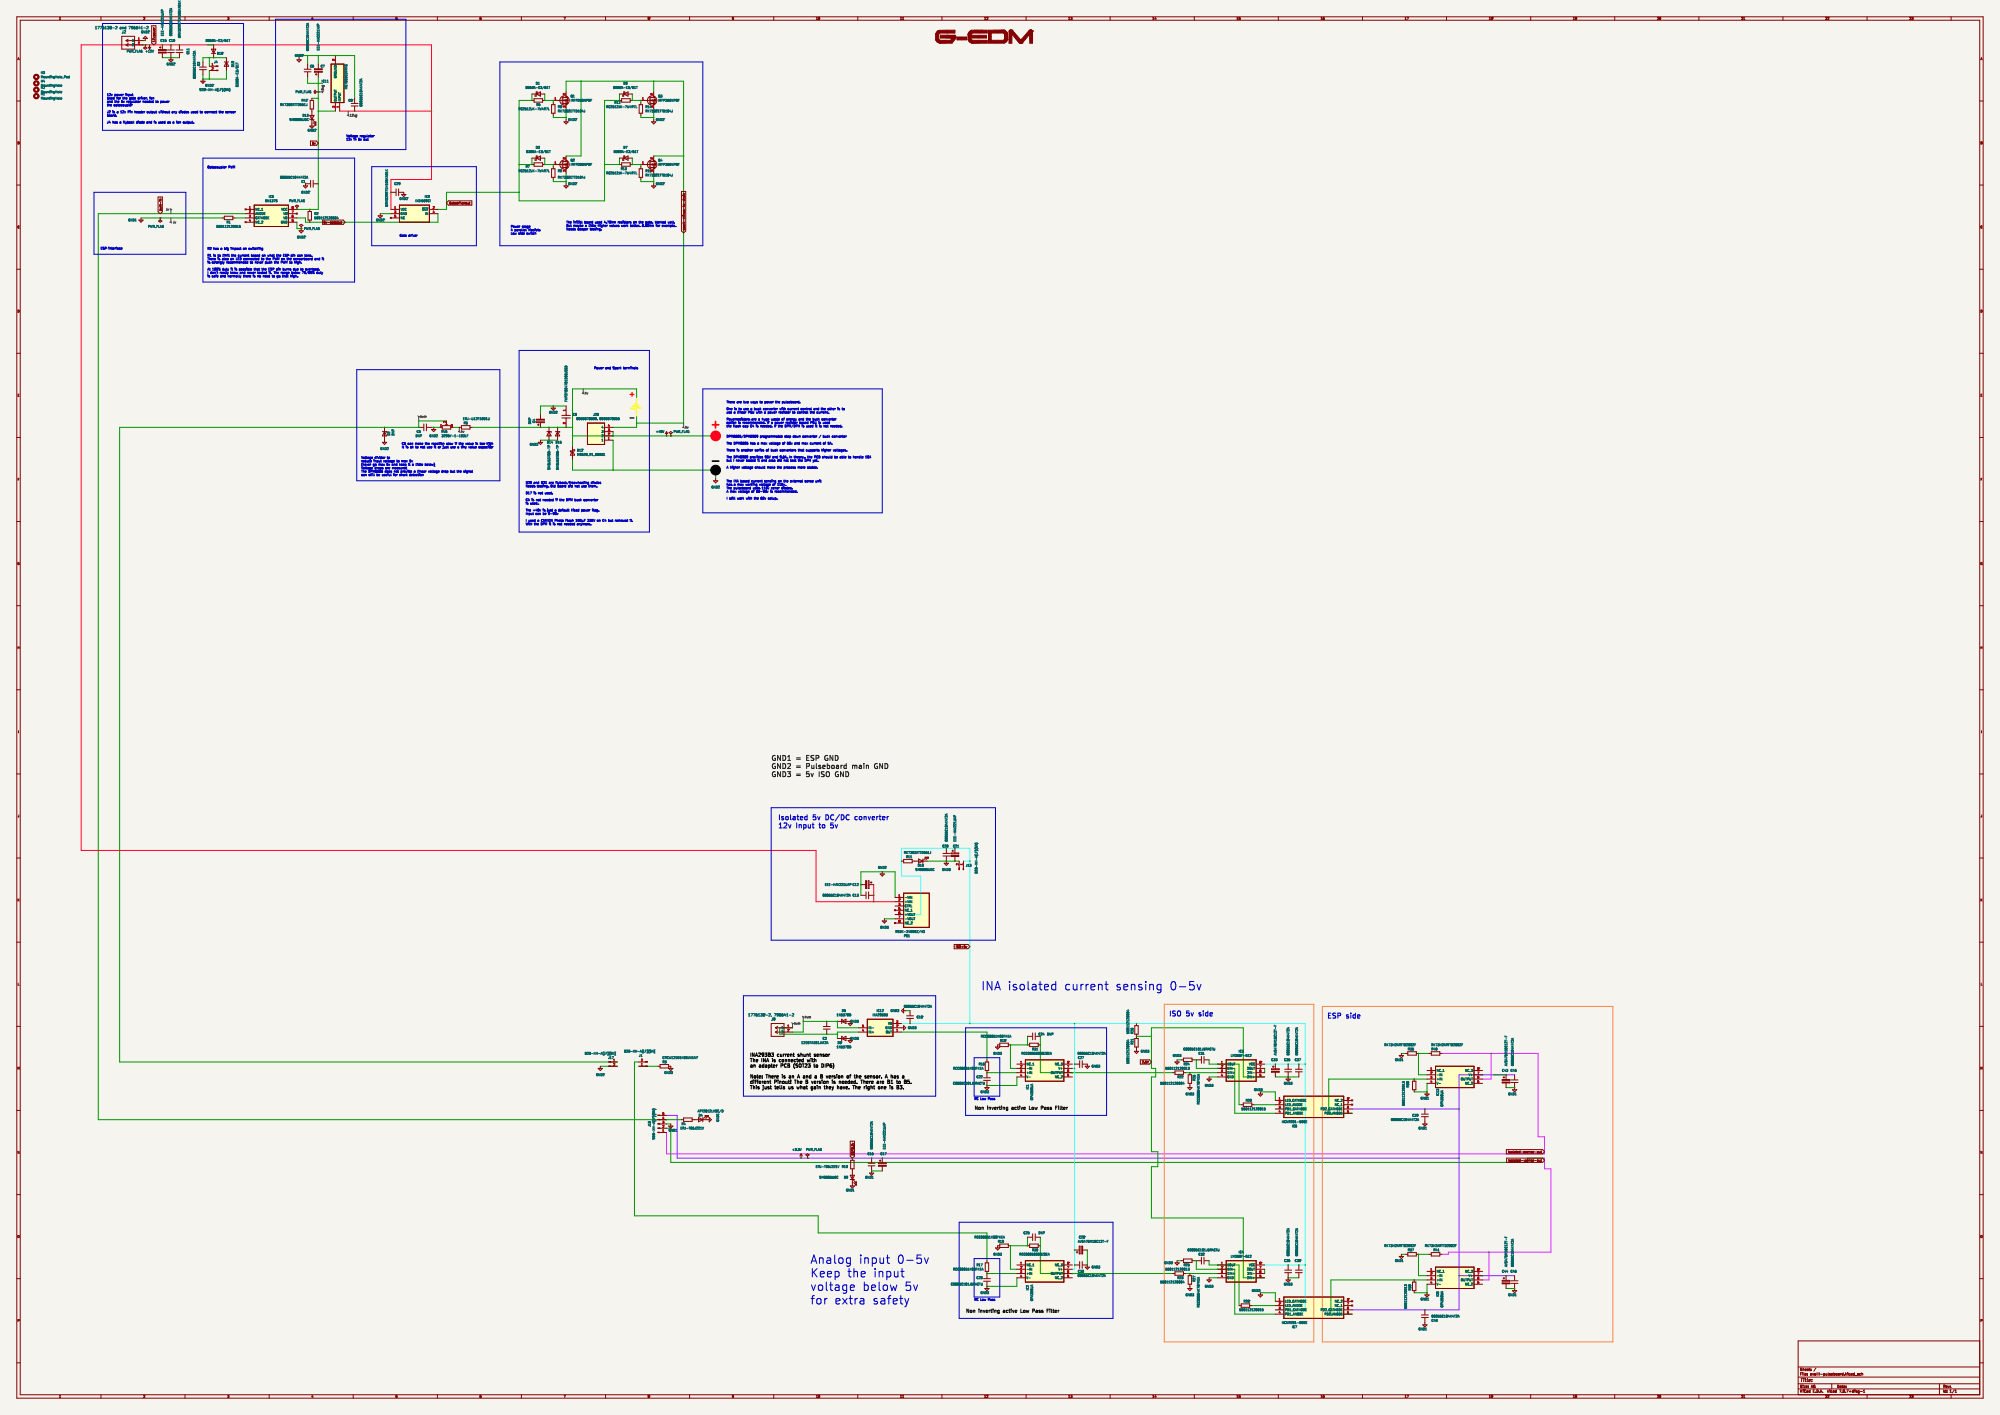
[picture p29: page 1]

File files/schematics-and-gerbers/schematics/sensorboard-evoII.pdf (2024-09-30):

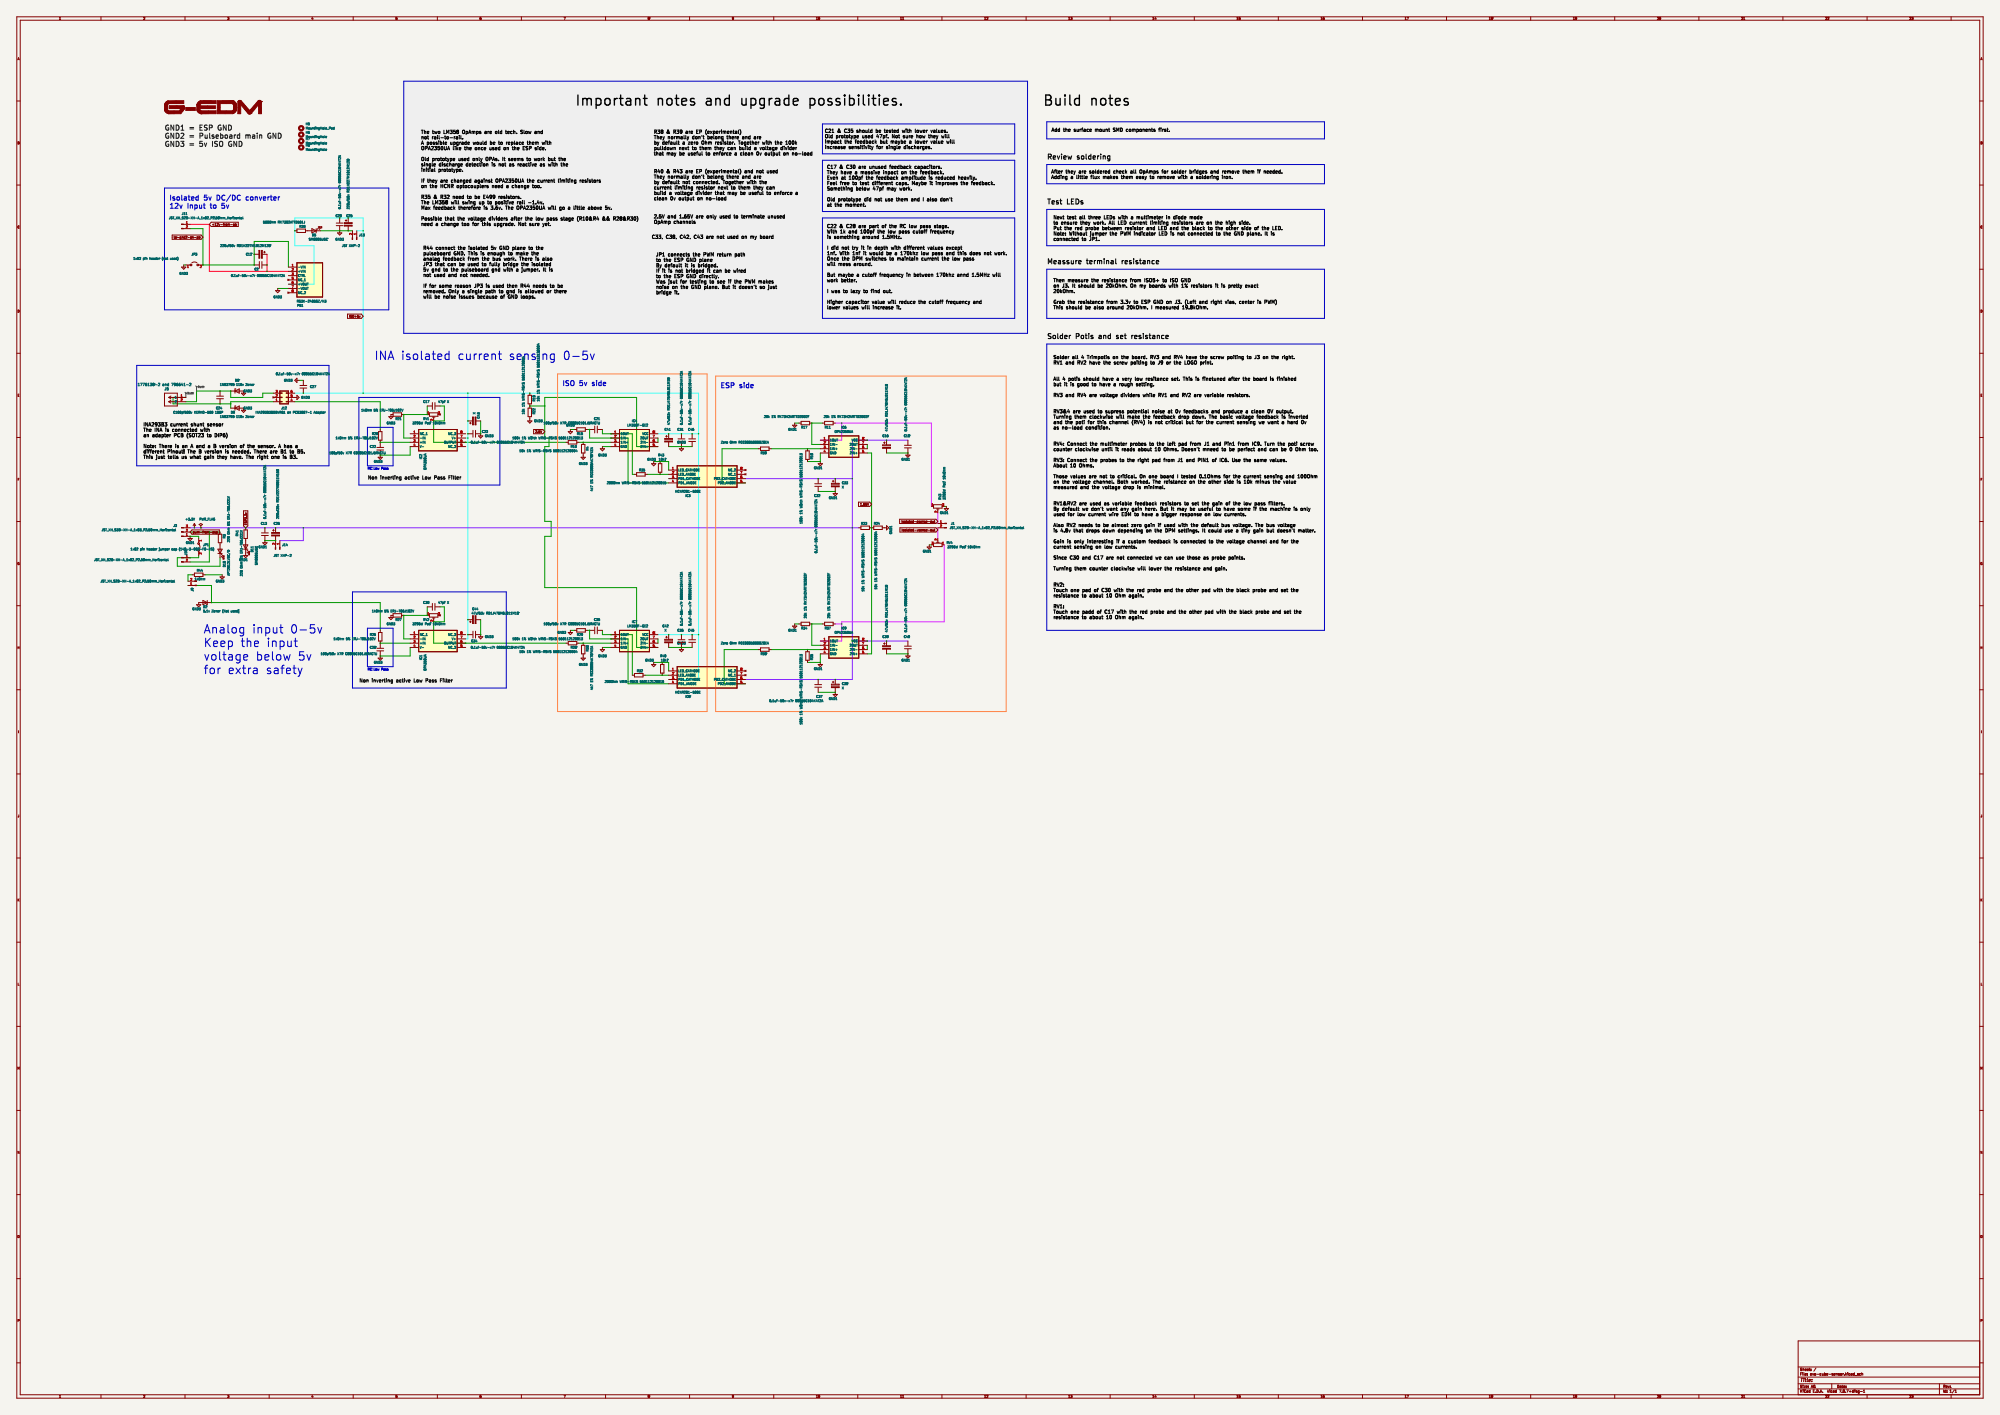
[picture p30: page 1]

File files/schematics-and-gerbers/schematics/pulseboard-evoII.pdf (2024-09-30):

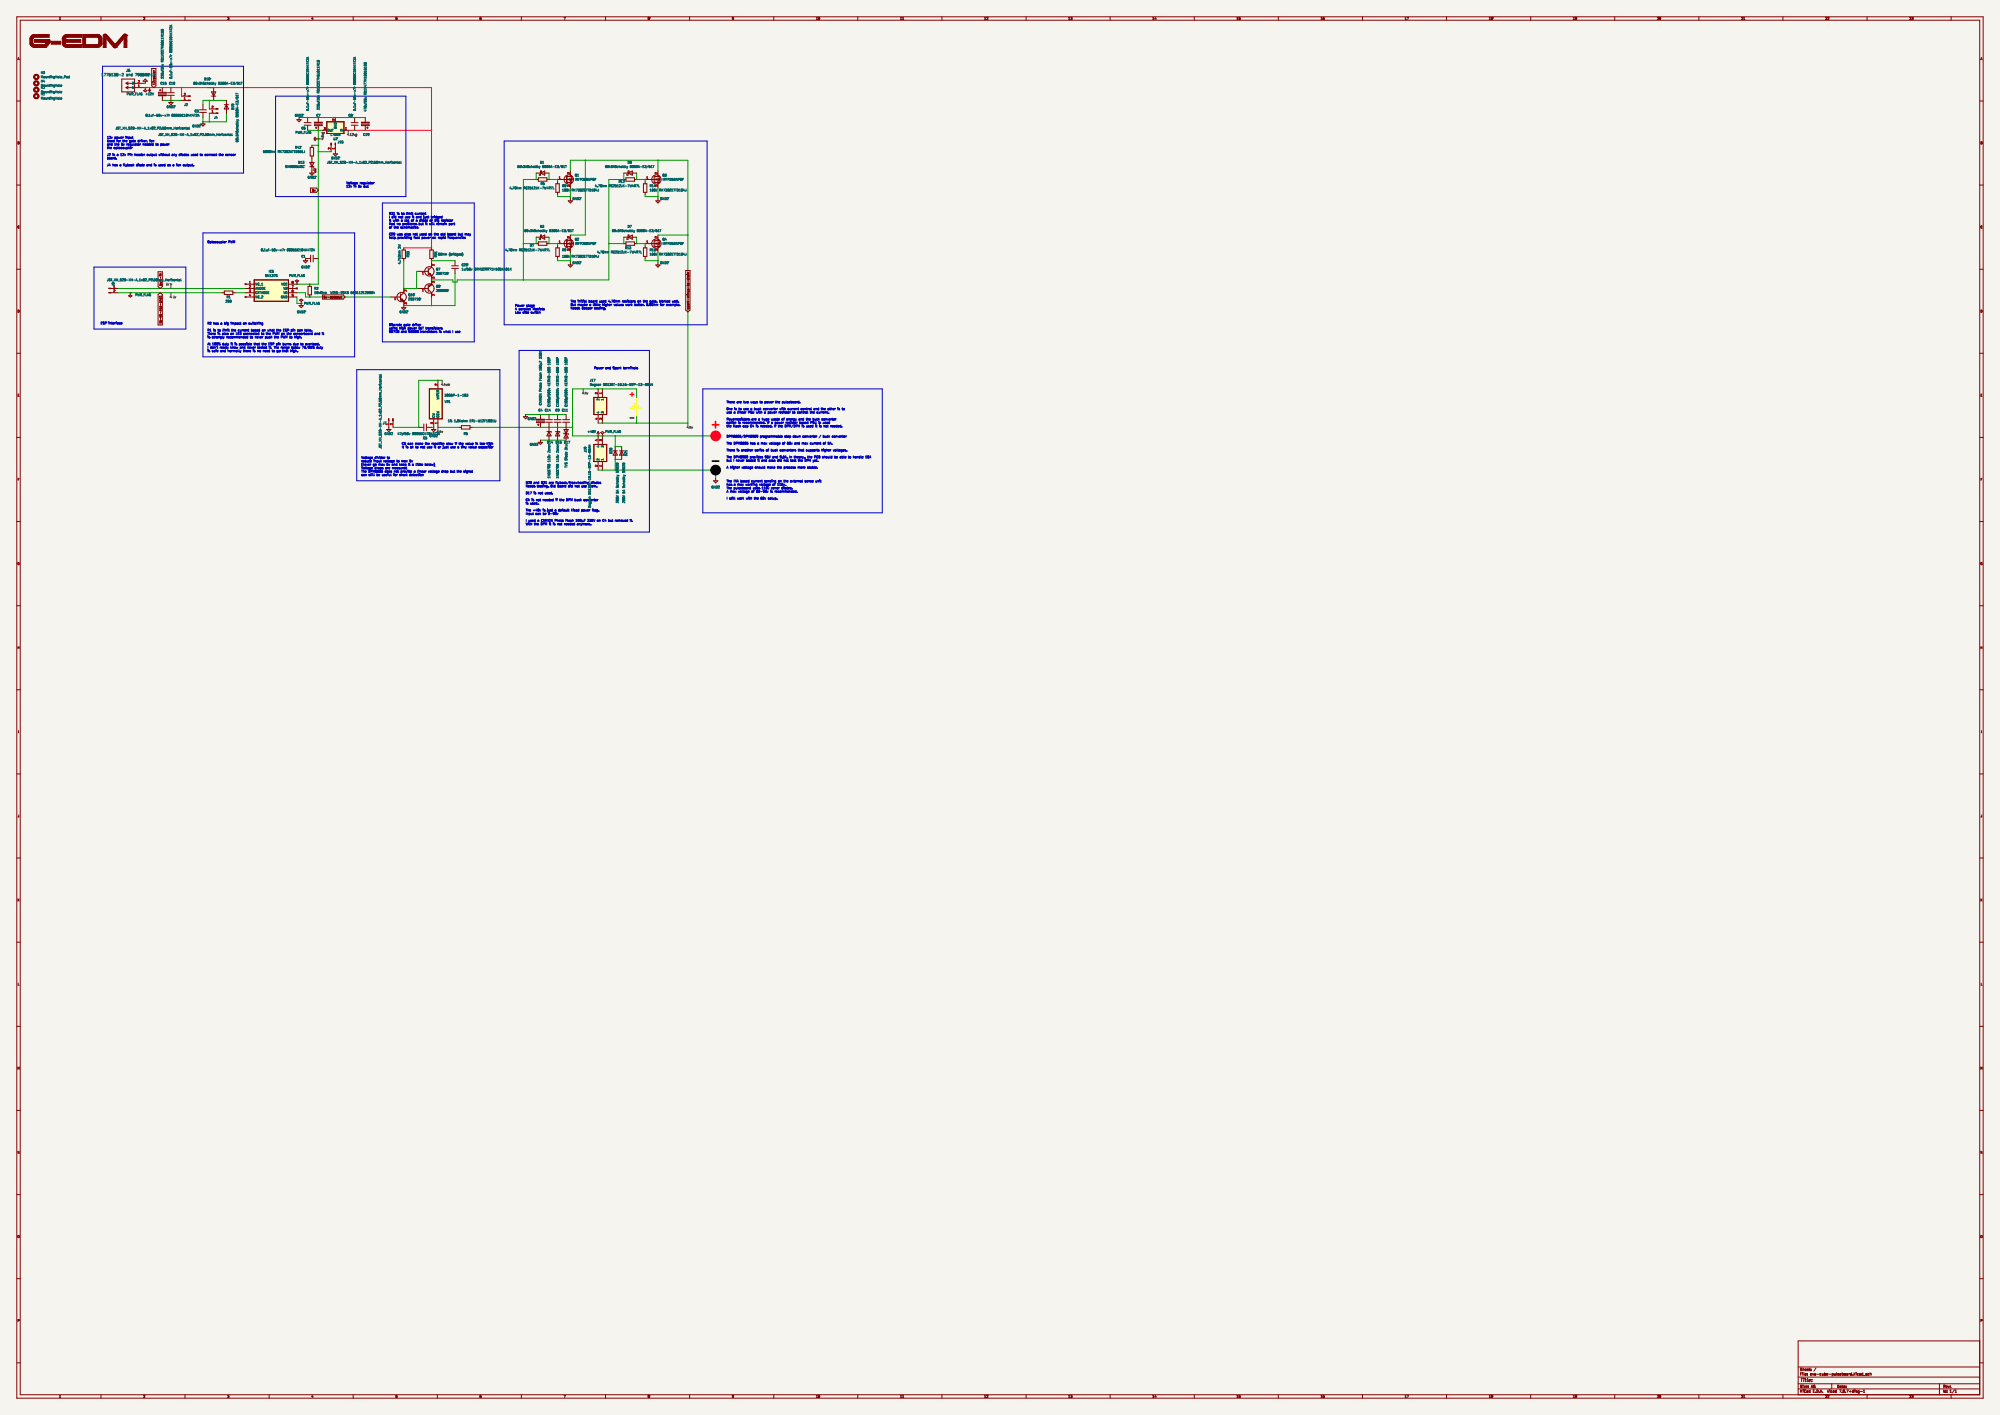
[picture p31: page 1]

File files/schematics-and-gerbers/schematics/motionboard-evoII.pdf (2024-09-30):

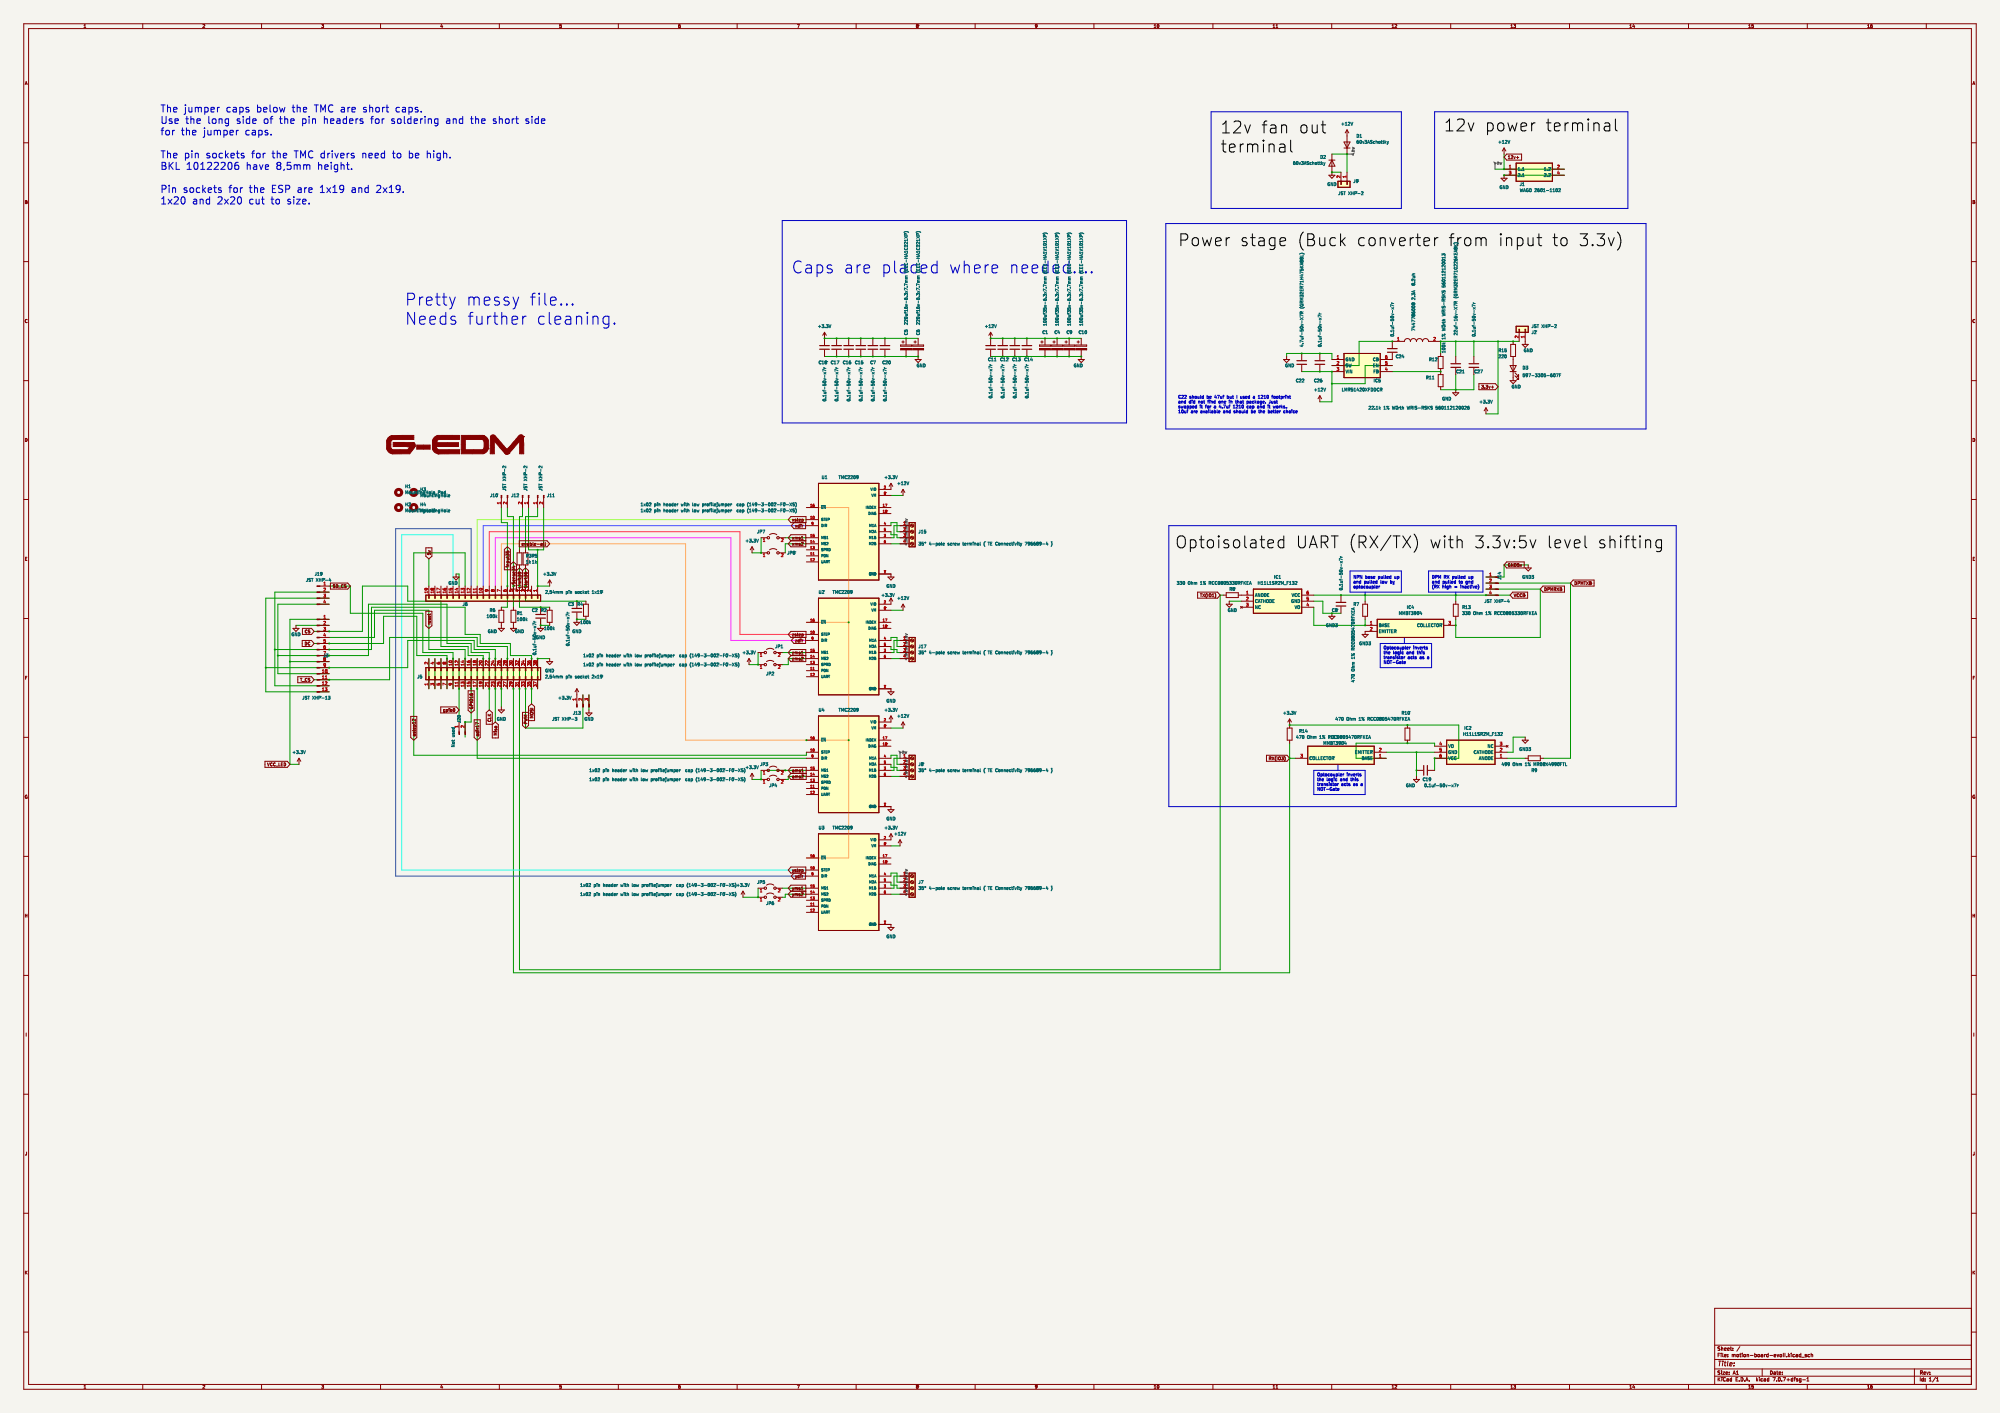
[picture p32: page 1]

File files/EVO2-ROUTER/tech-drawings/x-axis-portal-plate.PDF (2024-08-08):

030 12

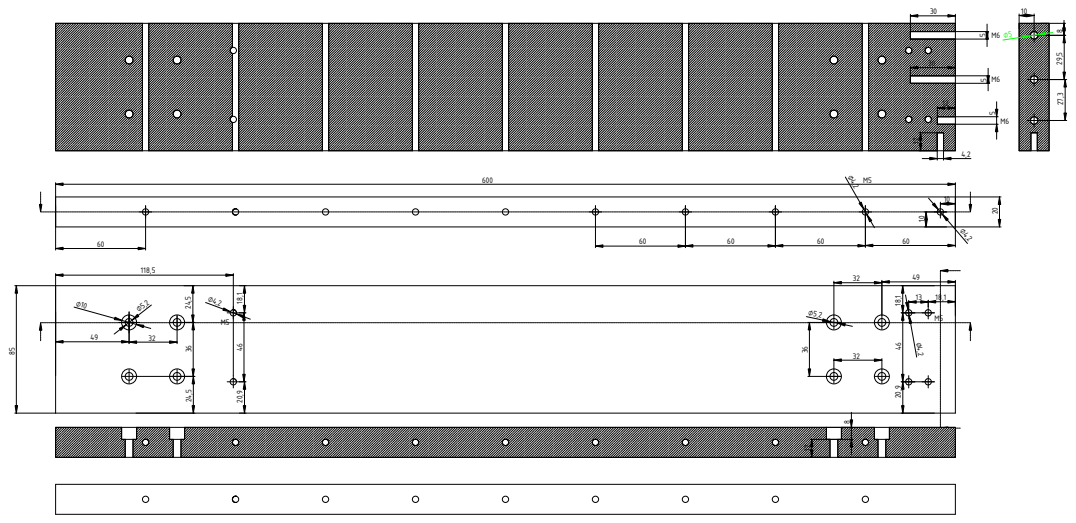
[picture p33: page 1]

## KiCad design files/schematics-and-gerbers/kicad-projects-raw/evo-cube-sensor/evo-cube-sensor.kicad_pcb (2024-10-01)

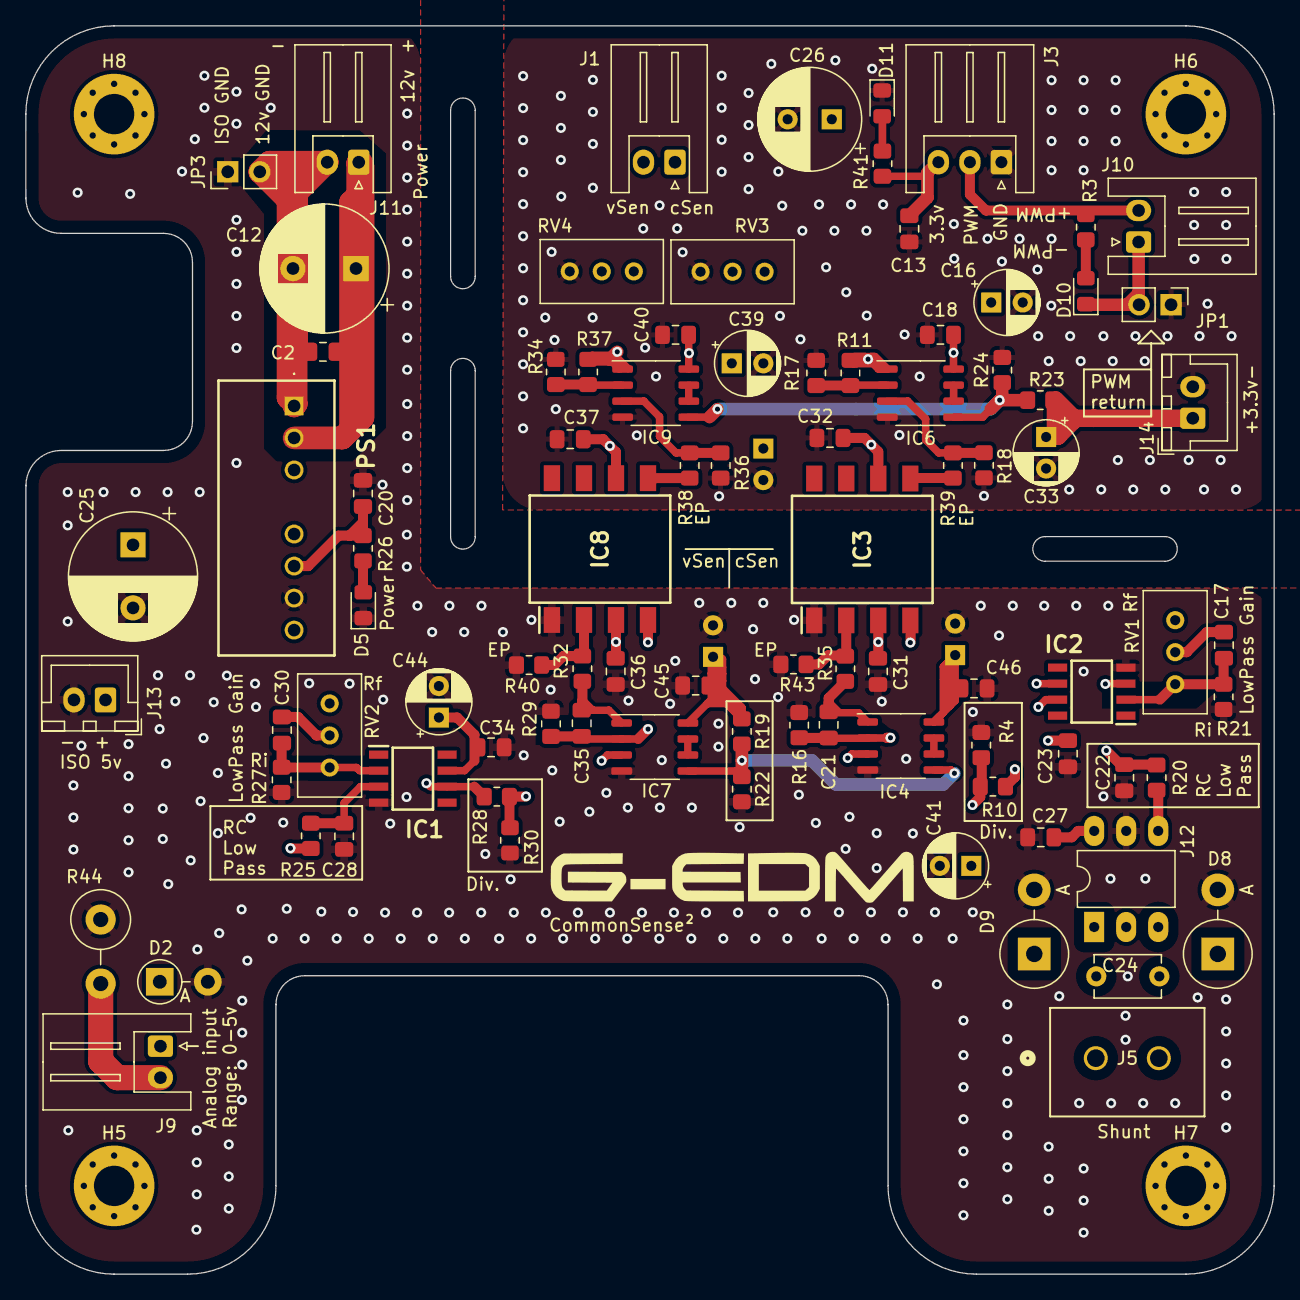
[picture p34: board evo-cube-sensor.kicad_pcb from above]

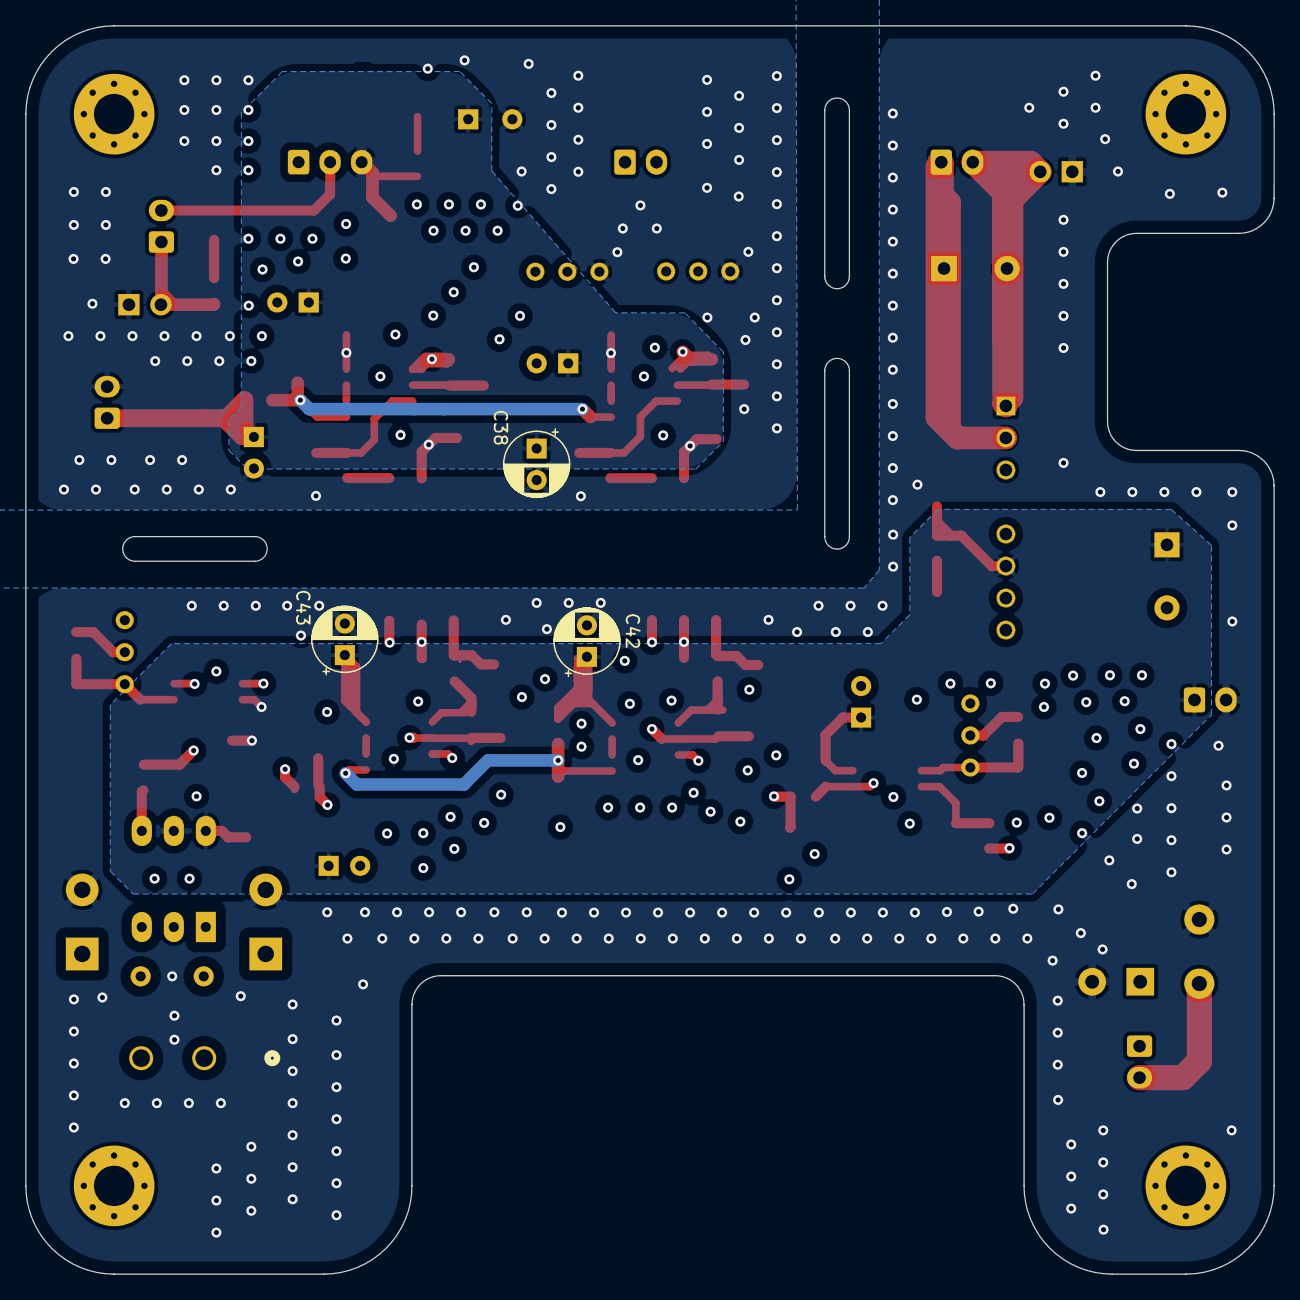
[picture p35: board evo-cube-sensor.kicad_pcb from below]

Board: 4 copper layers, 99.0 x 99.0 mm, 96 parts (3 on the bottom side), 46 nets.

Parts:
C2, C13, C18, C20, C23, C27, C31, C32, C34, C36, C37, C40, C45, C46: 0.1uf-50v-x7r 08055C104K4T2A; C_0805_2012Metric_Pad1.18x1.45mm_HandSolder
C12, C25: 220uf50v RD1H227M1012M128; CP_Radial_D10.0mm_P5.00mm
C16, C39, C41, C44: 47uf63v RD1J476M6L011M18; CP_Radial_D5.0mm_P2.50mm
C17, C30: 47pf X; C_0805_2012Metric_Pad1.18x1.45mm_HandSolder
C21, C22, C28, C35: 100pf50v X7R C0805C101J5RACTU; C_0805_2012Metric_Pad1.18x1.45mm_HandSolder
C24: C100pf500v KERKO-500 100P; C_Disc_D5.1mm_W3.2mm_P5.00mm
C26: 220uf35v RD1V227M0811M160; CP_Radial_D8.0mm_P3.50mm
C33, C38, C42, C43: X; CP_Radial_D5.0mm_P2.50mm
D2: 5.1v Zener (Not used); D_DO-41_SOD81_P3.81mm_Vertical_AnodeUp
D5, D11: SM0805UGC; LED_0805_2012Metric_Pad1.15x1.40mm_HandSolder
D8, D9: 1N5379B 110v Zener; D_DO-201_P5.08mm_Vertical_AnodeUp
D10: APT2012LVBC/D; LED_0805_2012Metric_Pad1.15x1.40mm_HandSolder
H5: MountingHole_Pad; MountingHole_3.2mm_M3_Pad_Via
H6, H7, H8: MountingHole; MountingHole_3.2mm_M3_Pad_Via
IC1, IC2: OPA350UA; SOIC127P600X175-8N
IC3, IC8: HCNR201-500E; SOP254P1230X400-8N
IC4, IC7: LM358F-GE2; SOP-8_3.9x4.9mm_P1.27mm
IC6, IC9: OPA2350UA; SOP-8_3.9x4.9mm_P1.27mm
J1, J9, J10, J11: JST_XH_S2B-XH-A_1x02_P2.50mm_Horizontal
J3: JST_XH_S3B-XH-A_1x03_P2.50mm_Horizontal
J5: 1776138-2 and 796641-2; CONN2_796643-2_TEC
J12: INA293B3QDBVRQ1 on PCB3007-1 Adapter; DIP-6_W7.62mm_LongPads
J13, J14: JST XHP-2; JST_XH_B2B-XH-A_1x02_P2.50mm_Vertical
JP1: Jumper_2_Bridged; PinHeader_1x02_P2.54mm_Vertical
JP3: 1x02 pin header jumper cap (149-3-002-F0-XS); PinHeader_1x02_P2.54mm_Vertical
PS1: RS3K-2405SZ/H3; RS3K2405SZH3
R3: 220; R_0805_2012Metric_Pad1.20x1.40mm_HandSolder
R4, R30: 4k7; R_0805_2012Metric_Pad1.20x1.40mm_HandSolder
R10, R19, R22, R23, R24, R28: 10k 1% WRIS-RSKS 560112120004; R_0805_2012Metric_Pad1.20x1.40mm_HandSolder
R11, R17, R34, R37: 20k RK73H2ARTTD2002F; R_0805_2012Metric_Pad1.20x1.40mm_HandSolder
R16, R18, R29, R36: 100k 1% Würth WRIS-RSKS 560112120013; R_0805_2012Metric_Pad1.20x1.40mm_HandSolder
R20, R21, R25, R27: 1kOhm 5% ERJ-T06J102V; R_0805_2012Metric_Pad1.20x1.40mm_HandSolder
R26: 560Ohm RK73B2ATTD561J; R_0805_2012Metric_Pad1.20x1.40mm_HandSolder
R32, R35: 200Ohm WRIS-RSKS 560112120015; R_0805_2012Metric_Pad1.20x1.40mm_HandSolder
R38, R39: Zero Ohm RCC08050000Z0EA; R_0805_2012Metric_Pad1.20x1.40mm_HandSolder
R40, R43: 10k?; R_0805_2012Metric_Pad1.20x1.40mm_HandSolder
R41: 220 Ohm 5% ERJ-T06J221V; R_0805_2012Metric_Pad1.20x1.40mm_HandSolder
R44: 1kOhm; R_Axial_DIN0414_L11.9mm_D4.5mm_P5.08mm_Vertical
RV1, RV2, RV3, RV4: 3296W Poti 10kOhm; Potentiometer_Bourns_3296W_Vertical

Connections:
1,65V: IC6.5 (2IN+), IC9.5 (2IN+), R23.2, R24.1
2.5V: IC4.5 (2IN+), IC7.5 (2IN+), R19.2, R22.1
+12v-from-pb: C2.1, C12.1, J11.1, PS1.2 (+VIN)
ESP3.3v: C13.1, C16.1, C18.1, C26.1, C32.1, C33.1, C37.1, C38.1, C39.1, C40.1, IC3.6 (PD2_CATHODE), IC6.8 (VCC), IC8.6 (PD2_CATHODE), IC9.8 (VCC), J3.3, J14.1, R23.1, R41.2
GND1: C13.2, C16.2, C18.2, C26.2, C32.2, C33.2, C37.2, C38.2, C39.2, C40.2, D11.1 (K), IC6.4 (GND), IC9.4 (GND), J3.1, J14.2, JP1.1 (A), R17.1, R18.1, R24.2, R34.1, R36.1, RV3.3, RV4.3
GND3: C20.2, C22.2, C23.2, C25.2, C27.1, C28.2, C31.1, C34.2, C36.1, C41.2, C42.2, C43.2, C44.2, C45.1, C46.1, D2.2 (A), D5.1 (K), D8.2 (A), D9.2 (A), IC1.4 (V-), IC2.4 (V-), IC3.1 (LED_CATHODE), IC4.4 (GND), IC7.4 (GND), IC8.1 (LED_CATHODE), J12.5, J13.2, JP3.1 (A), PS1.7 (-VOUT), R4.2, R16.1, R21.2, R22.2, R27.2, R29.1, R30.2, R40.2, R43.2, R44.1
ISO+5v: C20.1, C23.1, C25.1, C27.2, C31.2, C34.1, C36.2, C41.1, C42.1, C43.1, C44.1, C45.2, C46.2, IC1.7 (V+), IC2.7 (V+), IC3.3 (PD1_CATHODE), IC4.8 (VCC), IC7.8 (VCC), IC8.3 (PD1_CATHODE), J12.6, J13.1, PS1.6 (+VOUT), R19.1, R26.2
Isolated-csense-out: J1.1, RV3.2
Isolated-vsense-out: J1.2, RV4.2
unnamed: D2.1 (K), J9.1, R25.1
unnamed: D5.2 (A), R26.1
unnamed: C24.1, D8.1 (K), J5.2, J12.3
unnamed: C24.2, D9.1 (K), J5.1, J12.1
unnamed: D10.2 (A), R3.1
unnamed: D10.1 (K), J10.1, JP1.2 (B)
unnamed: D11.2 (A), R41.1
unnamed: C28.1, IC1.3 (+IN), R25.2
unnamed: C30.2, IC1.2 (-IN), R27.1, RV2.1
unnamed: C30.1, IC1.6 (OUTPUT), R28.2, RV2.2
unnamed: C22.1, IC2.3 (+IN), R20.2
unnamed: C17.2, IC2.2 (-IN), R21.1, RV1.1
unnamed: C17.1, IC2.6 (OUTPUT), R10.2, RV1.2
unnamed: IC3.2 (LED_ANODE), R35.1, R43.1
unnamed: C21.1, IC3.4 (PD1_ANODE), IC4.2 (1IN-), R16.2
unnamed: IC3.5 (PD2_ANODE), R39.1
unnamed: IC4.3 (1IN+), R4.1, R10.1
unnamed: C21.2, IC4.1 (1OUT), R35.2
unnamed: IC4.6 (2IN-), IC4.7 (2OUT)
unnamed: IC6.3 (1IN+), R18.2, R39.2
unnamed: IC6.2 (1IN-), R11.1, R17.2
unnamed: IC6.1 (1OUT), R11.2, RV3.1
unnamed: IC6.6 (2IN-), IC6.7 (2OUT)
unnamed: IC7.3 (1IN+), R28.1, R30.1
unnamed: C35.1, IC7.2 (1IN-), IC8.4 (PD1_ANODE), R29.2
unnamed: C35.2, IC7.1 (1OUT), R32.2
unnamed: IC7.6 (2IN-), IC7.7 (2OUT)
unnamed: IC8.2 (LED_ANODE), R32.1, R40.1
unnamed: IC8.5 (PD2_ANODE), R38.1
unnamed: IC9.3 (1IN+), R36.2, R38.2
unnamed: IC9.2 (1IN-), R34.2, R37.1
unnamed: IC9.1 (1OUT), R37.2, RV4.1
unnamed: IC9.6 (2IN-), IC9.7 (2OUT)
unnamed: J9.2, R44.2
unnamed: J12.4, R20.1
pwm-from-esp: J3.2, J10.2, R3.2
to-gnd2-on-pb: C2.2, C12.2, J11.2, JP3.2 (B), PS1.1 (-VIN)

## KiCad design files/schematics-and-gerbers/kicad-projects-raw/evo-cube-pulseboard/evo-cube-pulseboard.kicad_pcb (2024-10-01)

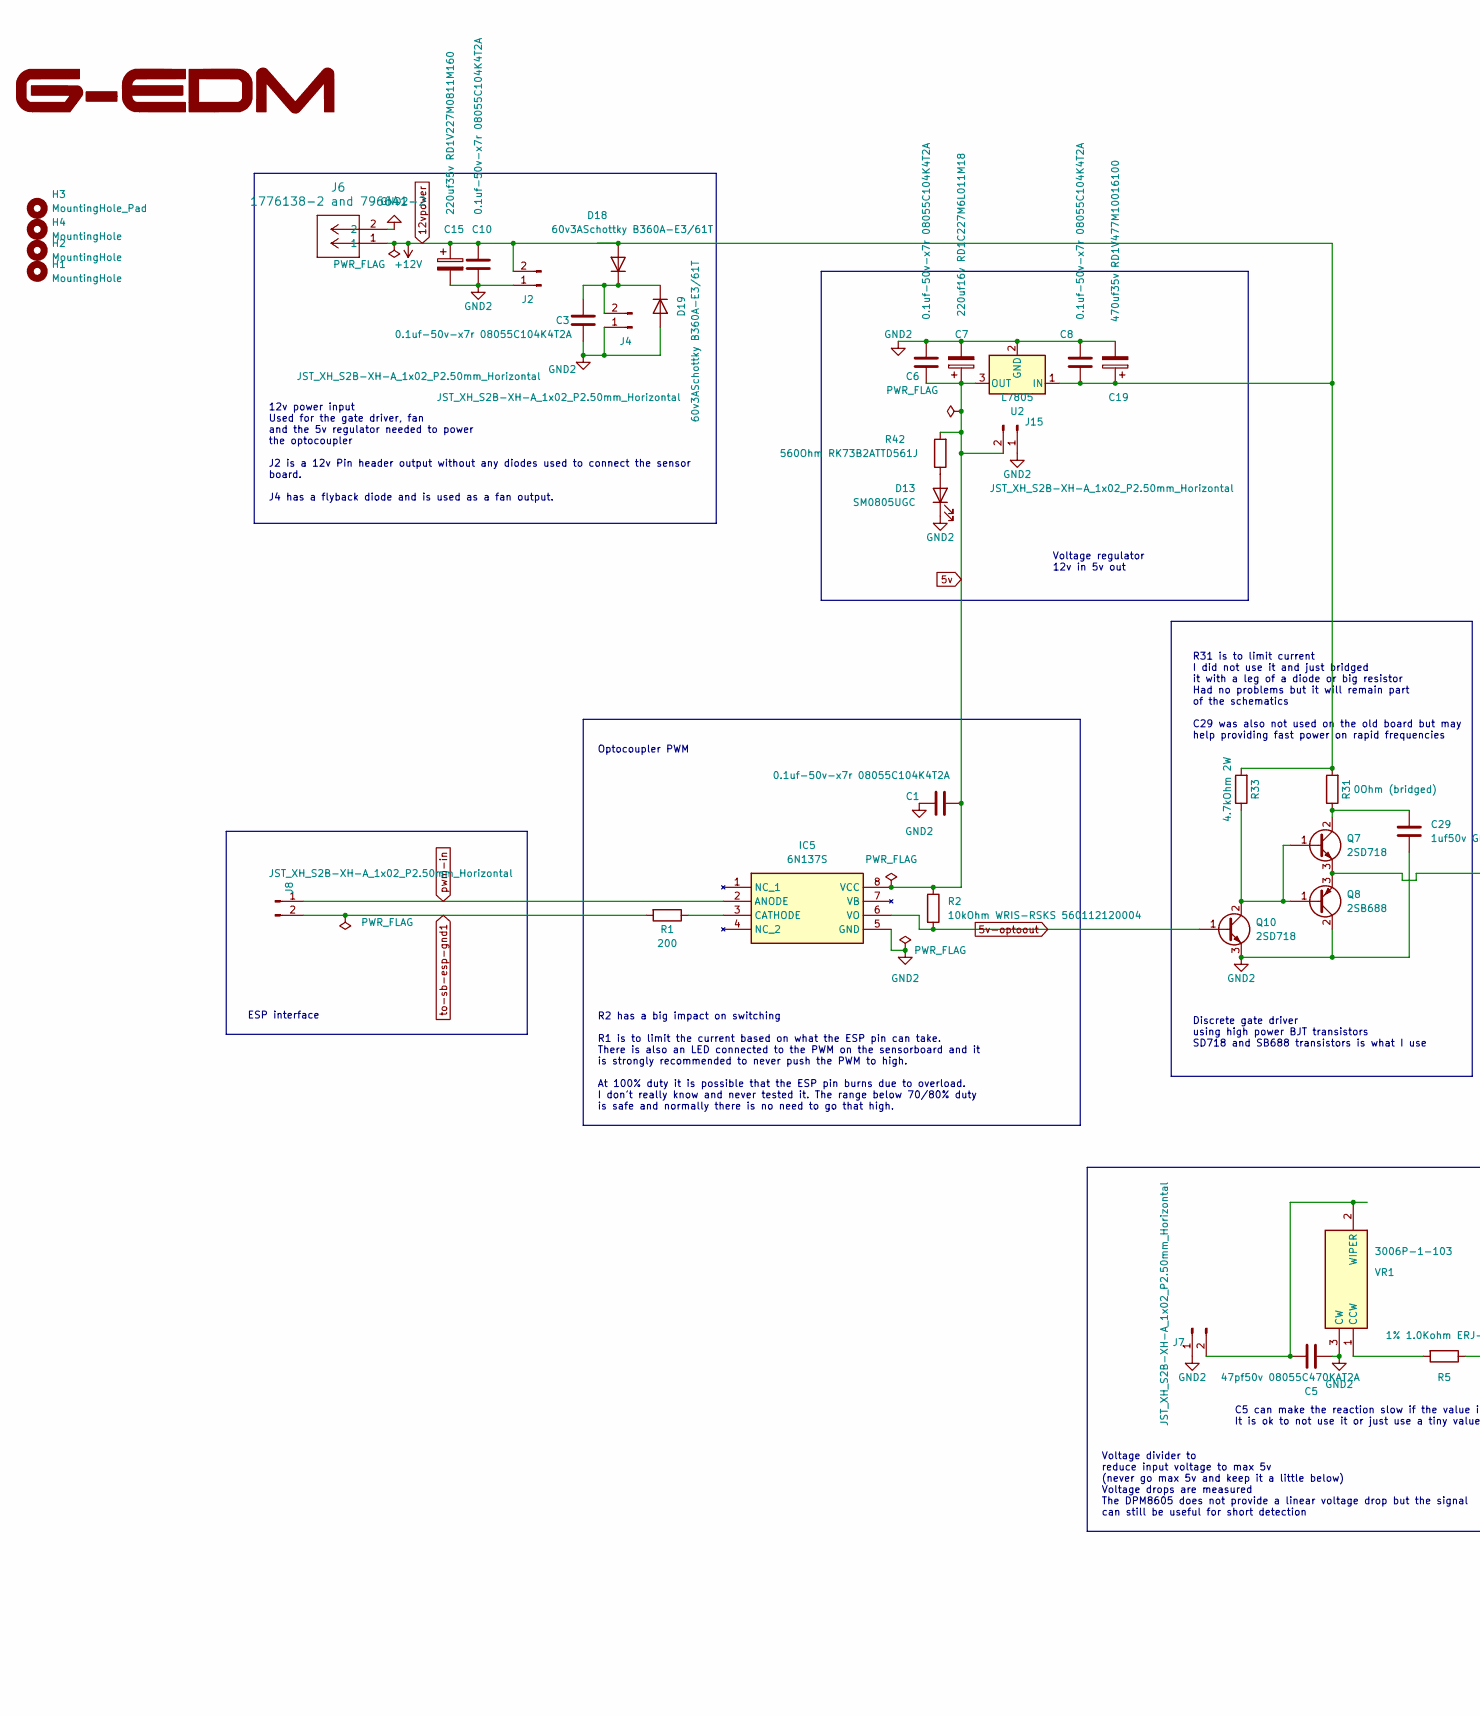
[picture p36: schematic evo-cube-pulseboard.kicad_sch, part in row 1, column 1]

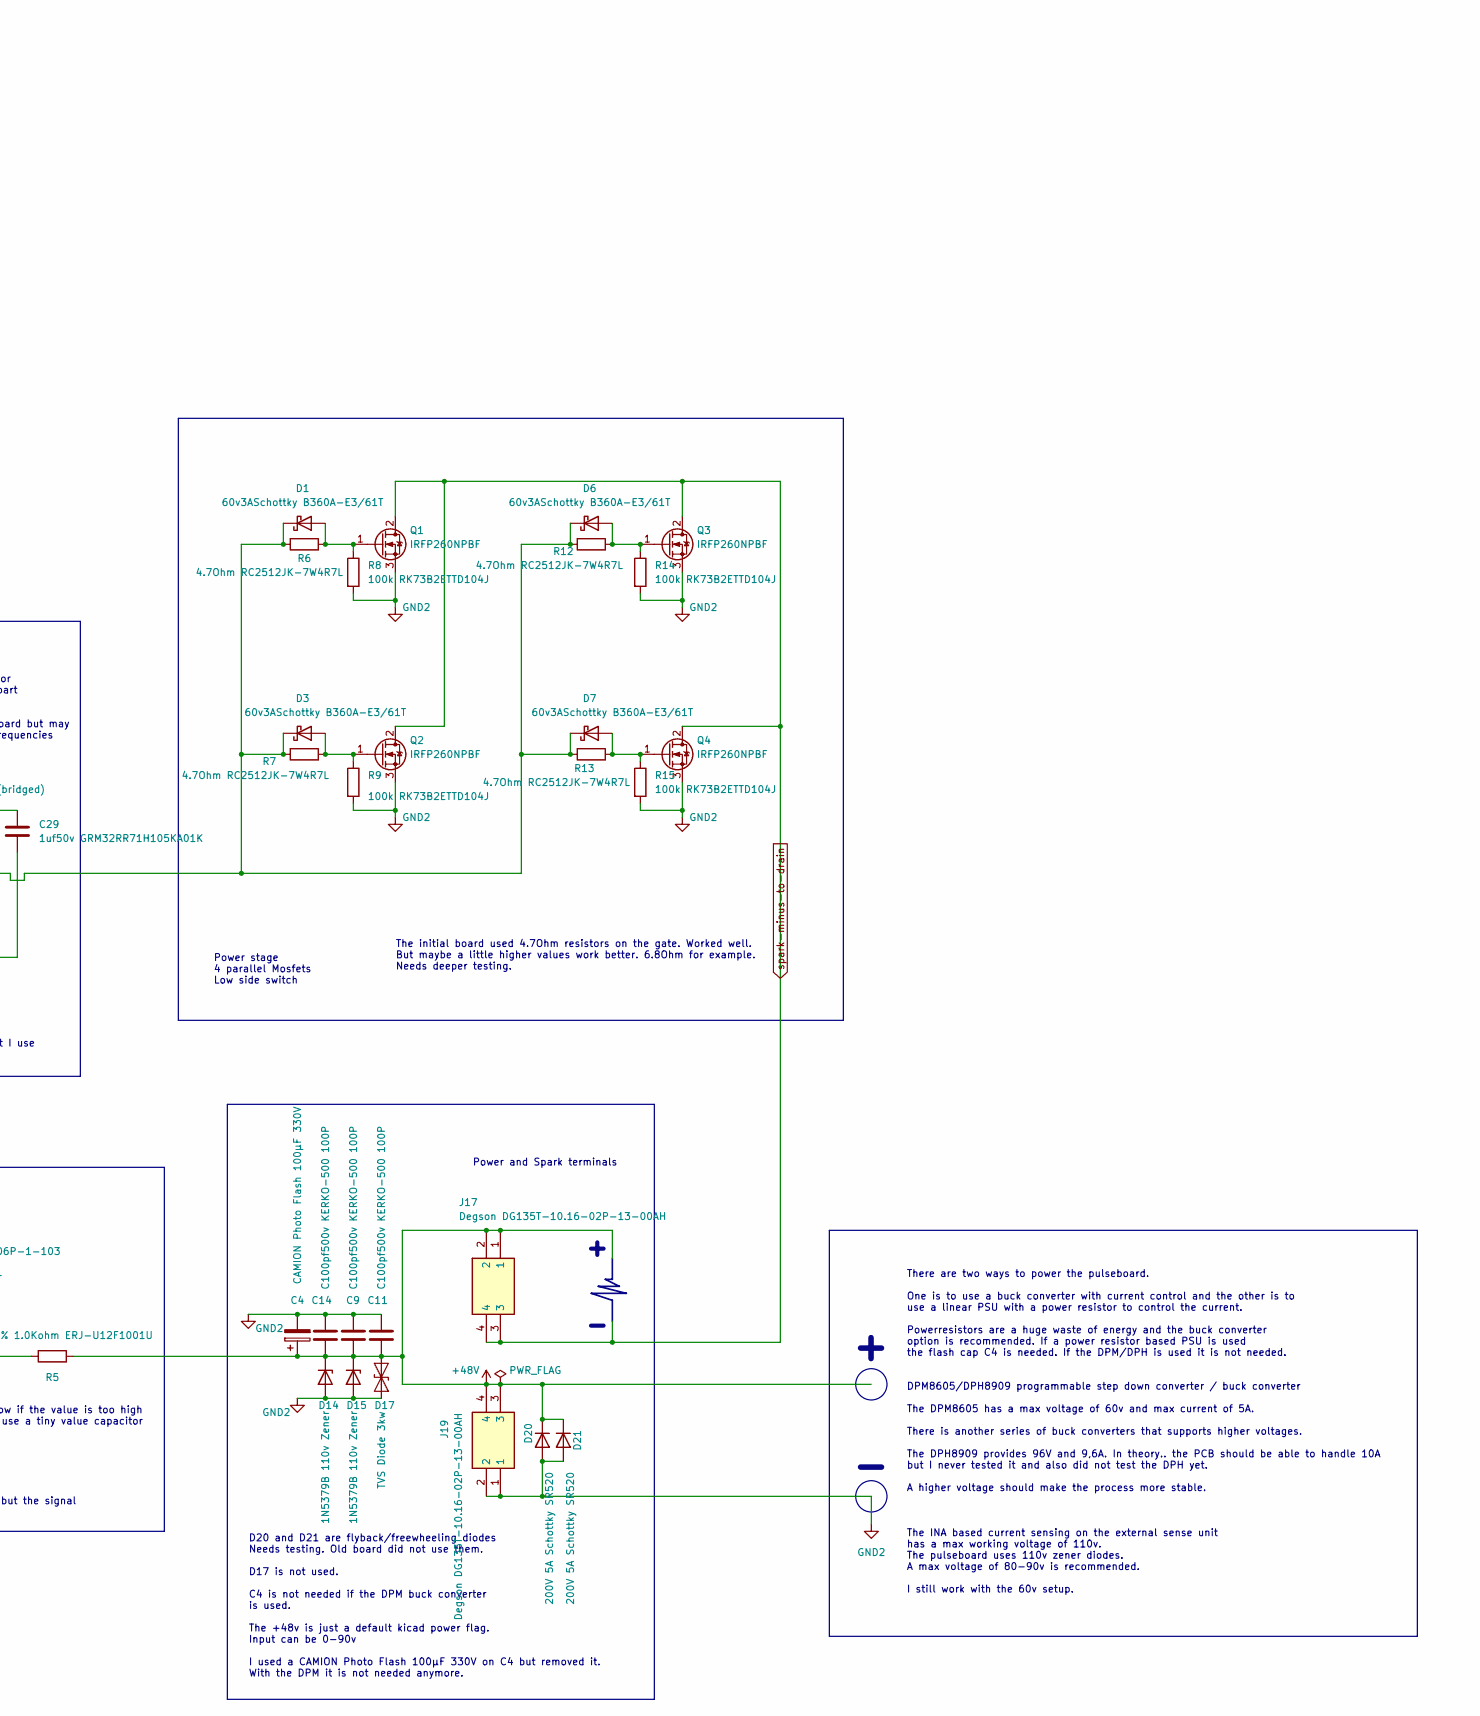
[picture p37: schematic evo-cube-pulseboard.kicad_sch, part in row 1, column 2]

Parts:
C1, C3, C6, C8, C10: 0.1uf-50v-x7r 08055C104K4T2A; C_0805_2012Metric_Pad1.18x1.45mm_HandSolder
C4: CAMION Photo Flash 100µF 330V; CP_Radial_D14.0mm_P5.00mm
C5: 47pf50v 08055C470KAT2A; C_1206_3216Metric_Pad1.33x1.80mm_HandSolder
C7: 220uf16v RD1C227M6L011M18; CP_Radial_D6.3mm_P2.50mm
C9, C11, C14: C100pf500v KERKO-500 100P; C_Disc_D5.0mm_W2.5mm_P5.00mm
C15: 220uf35v RD1V227M0811M160; CP_Radial_D8.0mm_P3.50mm
C19: 470uf35v RD1V477M10016100; CP_Radial_D10.0mm_P5.00mm
C29: 1uf50v GRM32RR71H105KA01K; C_1210_3225Metric_Pad1.33x2.70mm_HandSolder
D1, D3, D6, D7, D18, D19: 60v3ASchottky B360A-E3/61T; D_SMA_Handsoldering
D13: SM0805UGC; LED_0805_2012Metric_Pad1.15x1.40mm_HandSolder
D14, D15: 1N5379B 110v Zener; D_DO-201_P5.08mm_Vertical_AnodeUp
D17: TVS Diode 3kw; D_SMC_Handsoldering
D20, D21: 200V 5A Schottky SR520; D_DO-201_P5.08mm_Vertical_AnodeUp
H1, H2, H4: MountingHole; MountingHole_3.2mm_M3_Pad_Via
H3: MountingHole_Pad; MountingHole_3.2mm_M3_Pad_Via
IC5: 6N137S; SOP254P1016X460-8N; Manufacturer_Part_Number 6N136S; Mouser Part Number 859-6N136S
J2, J4, J7, J8, J15: JST_XH_S2B-XH-A_1x02_P2.50mm_Horizontal
J6: 1776138-2 and 796641-2; CONN2_796643-2_TEC
J17, J19: Degson DG135T-10.16-02P-13-00AH; DEGSONDG135T101602P1300AH; Manufacturer_Part_Number DEGSON DG135T-10.16-02P-13-00AH
Q1, Q2, Q3, Q4: IRFP260NPBF; TO-247-3_Horizontal_TabUp
Q7, Q10: 2SD718; TO-3PB-3_Vertical
Q8: 2SB688; TO-3PB-3_Vertical
R1: 200; R_0805_2012Metric_Pad1.20x1.40mm_HandSolder
R2: 10kOhm WRIS-RSKS 560112120004; R_0805_2012Metric_Pad1.20x1.40mm_HandSolder
R5: 1% 1.0Kohm ERJ-U12F1001U; R_1812_4532Metric_Pad1.30x3.40mm_HandSolder
R6, R7, R12, R13: 4.7Ohm RC2512JK-7W4R7L; R_2512_6332Metric_Pad1.40x3.35mm_HandSolder
R8, R9, R14, R15: 100k RK73B2ETTD104J; R_1210_3225Metric
R31: 0Ohm (bridged); R_Axial_DIN0414_L11.9mm_D4.5mm_P5.08mm_Vertical
R33: 4.7kOhm 2W; R_Axial_DIN0411_L9.9mm_D3.6mm_P5.08mm_Vertical
R42: 560Ohm RK73B2ATTD561J; R_0805_2012Metric_Pad1.20x1.40mm_HandSolder
U2: L7805; TO255P460X1020X2008-3P
VR1: 3006P-1-103; 3006P1103; Manufacturer_Part_Number 3006P-1-103; Mouser Part Number 652-3006P-1-103

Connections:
5v: C1.1, C6.1, C7.1, IC5.8 (VCC), J15.2, R2.1, R42.2, U2.3 (OUT)
5v-optoout: IC5.6 (VO), Q10.1 (B), R2.2
12vpower: C8.1, C10.1, C15.1, C19.1, D18.2 (A), J2.2, J6.1, R31.2, R33.2, U2.1 (IN)
+48V: C4.1, C9.1, C11.1, C14.1, D14.1 (K), D15.1 (K), D17.1 (A1), D20.1 (K), D21.1 (K), J17.1, J17.2, J19.3, J19.4, R5.1
GND2: C1.2, C3.1, C4.2, C5.2, C6.2, C7.2, C8.2, C9.2, C10.2, C11.2, C14.2, C15.2, C19.2, C29.2, D13.1 (K), D14.2 (A), D15.2 (A), D17.2 (A2), D19.2 (A), D20.2 (A), D21.2 (A), IC5.5 (GND), J2.1, J4.1, J6.2, J7.1, J15.1, J19.1, J19.2, Q1.3 (S), Q2.3 (S), Q3.3 (S), Q4.3 (S), Q8.2 (C), Q10.3 (E), R8.2, R9.2, R14.2, R15.2, U2.2 (GND), VR1.3 (CW)
unnamed: D1.2 (A), Q1.1 (G), R6.1, R8.1
unnamed: D1.1 (K), D3.1 (K), D6.1 (K), D7.1 (K), Q7.3 (E), Q8.3 (E), R6.2, R7.2, R12.2, R13.2
unnamed: D3.2 (A), Q2.1 (G), R7.1, R9.1
unnamed: D6.2 (A), Q3.1 (G), R12.1, R14.1
unnamed: D7.2 (A), Q4.1 (G), R13.1, R15.1
unnamed: D13.2 (A), R42.1
unnamed: C3.2, D18.1 (K), D19.1 (K), J4.2
unnamed: IC5.3 (CATHODE), R1.1
unnamed: C5.1, J7.2, VR1.2 (WIPER)
unnamed: C29.1, Q7.2 (C), R31.1
unnamed: Q7.1 (B), Q8.1 (B), Q10.2 (C), R33.1
unnamed: R5.2, VR1.1 (CCW)
pwm-in: IC5.2 (ANODE), J8.1
spark-minus-to-drain: J17.3, J17.4, Q1.2 (D), Q2.2 (D), Q3.2 (D), Q4.2 (D)
to-sb-esp-gnd1: J8.2, R1.2

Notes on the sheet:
There are two ways to power the pulseboard. One is to use a buck converter with current control and the other is to use a linear PSU with a power resistor to control the current. Powerresistors are a huge waste of energy and the buck converter option is recommended. If a power resistor based PSU is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
C5 can make the reaction slow if the value is too high It is ok to not use it or just use a tiny value capacitor
Power stage 4 parallel Mosfets Low side switch
R31 is to limit current I did not use it and just bridged it with a leg of a diode or big resistor Had no problems but it will remain part of the schematics C29 was also not used on the old board but may help providing fast power on rapid frequencies
Optocoupler PWM
Voltage divider to reduce input voltage to max 5v (never go max 5v and keep it a little below) Voltage drops are measured The DPM8605 does not provide a linear voltage drop but the signal can still be useful for short detection
Power and Spark terminals
R2 has a big impact on switching R1 is to limit the current based on what the ESP pin can take. There is also an LED connected to the PWM on the sensorboard and it is strongly recommended to never push the PWM to high. At 100% duty it is possible that the ESP pin burns due to overload. I don't real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
12v power input Used for the gate driver, fan and the 5v regulator needed to power the optocoupler J2 is a 12v Pin header output without any diodes used to connect the sensor board. J4 has a flyback diode and is used as a fan output.
Discrete gate driver using high power BJT transistors SD718 and SB688 transistors is what I use
D20 and D21 are flyback/freewheeling diodes Needs testing. Old board did not use them. D17 is not used. C4 is not needed if the DPM buck converter is used. The +48v is just a default kicad power flag. Input can be 0-90v I used a CAMION Photo Flash 100µF 330V on C4 but removed it. With the DPM it is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
Voltage regulator 12v in 5v out
The initial board used 4.7Ohm resistors on the gate. Worked well. But maybe a little higher values work better. 6.8Ohm for example. Needs deeper testing.
ESP interface

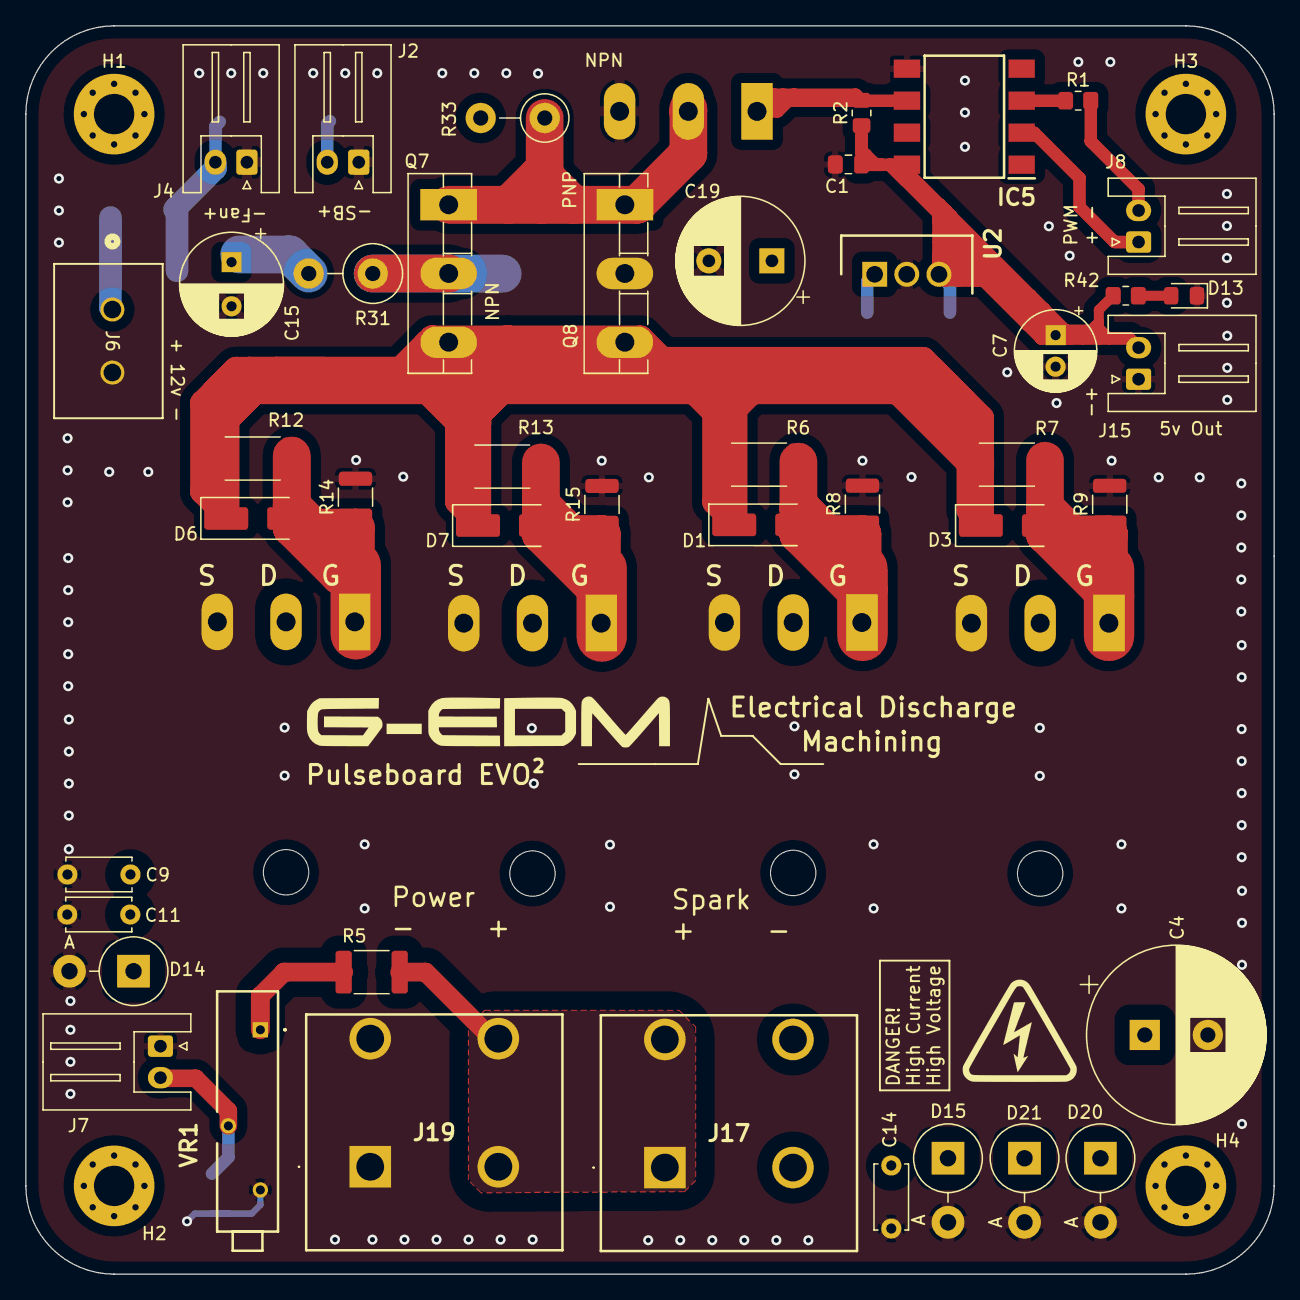
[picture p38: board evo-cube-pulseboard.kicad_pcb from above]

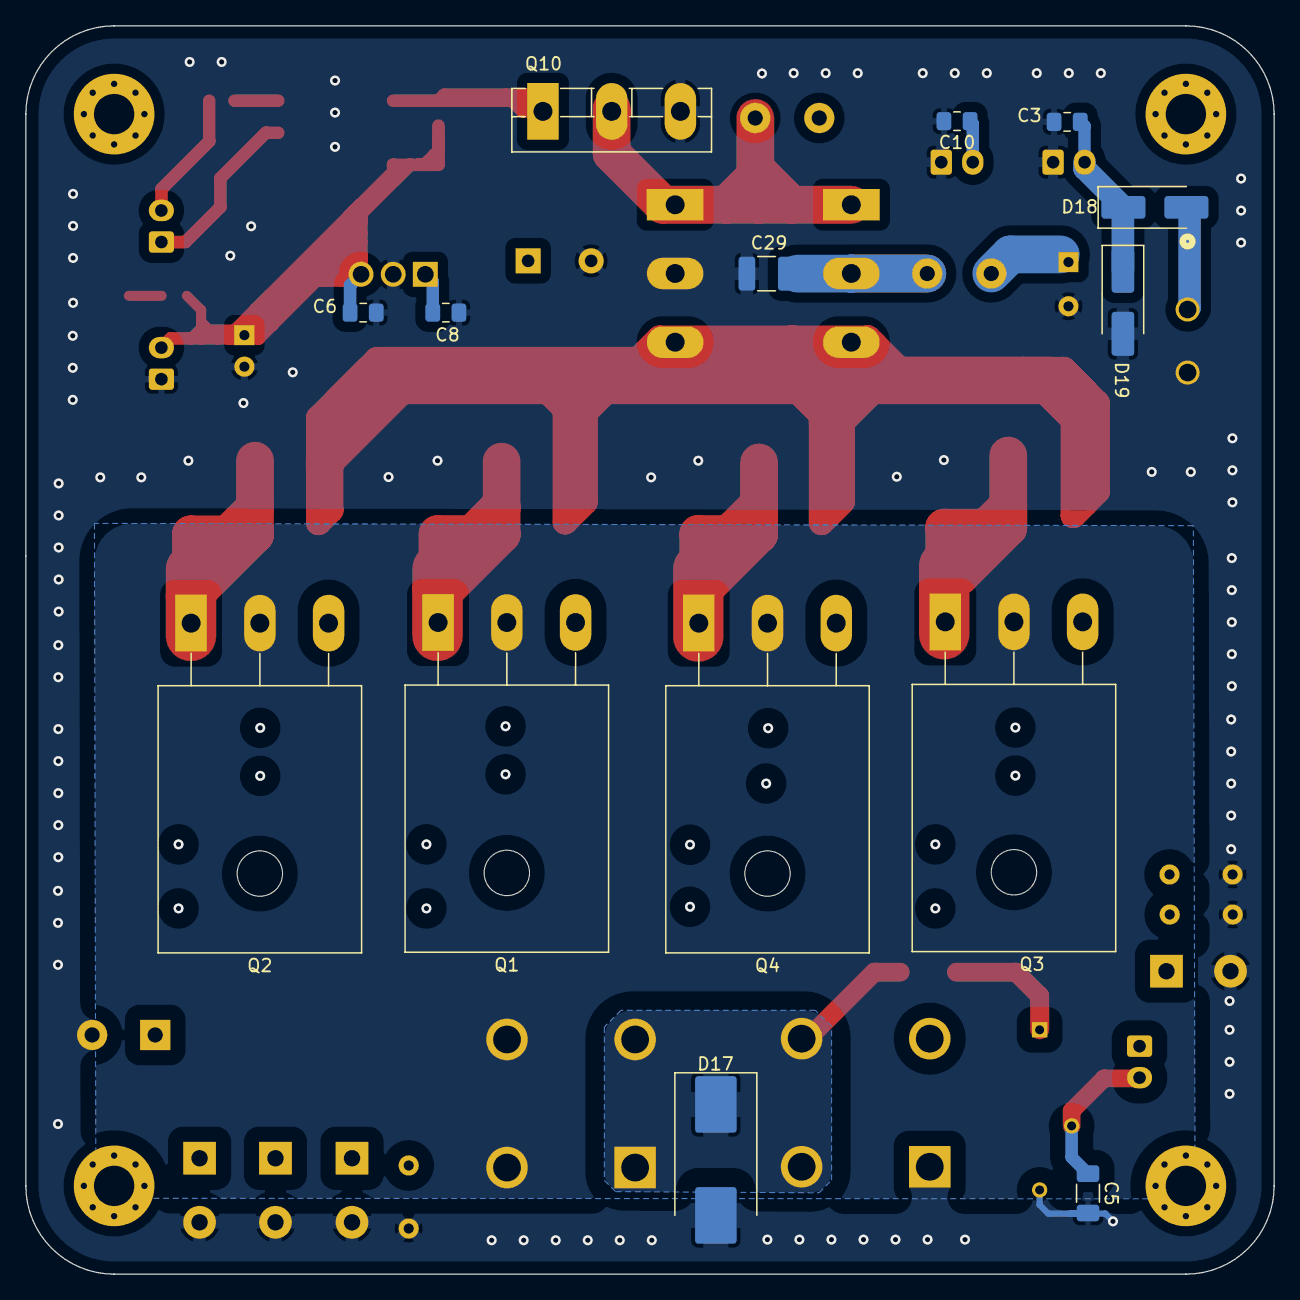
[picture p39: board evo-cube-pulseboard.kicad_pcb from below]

Board: 4 copper layers, 99.0 x 99.0 mm, 62 parts (14 on the bottom side), 20 nets.

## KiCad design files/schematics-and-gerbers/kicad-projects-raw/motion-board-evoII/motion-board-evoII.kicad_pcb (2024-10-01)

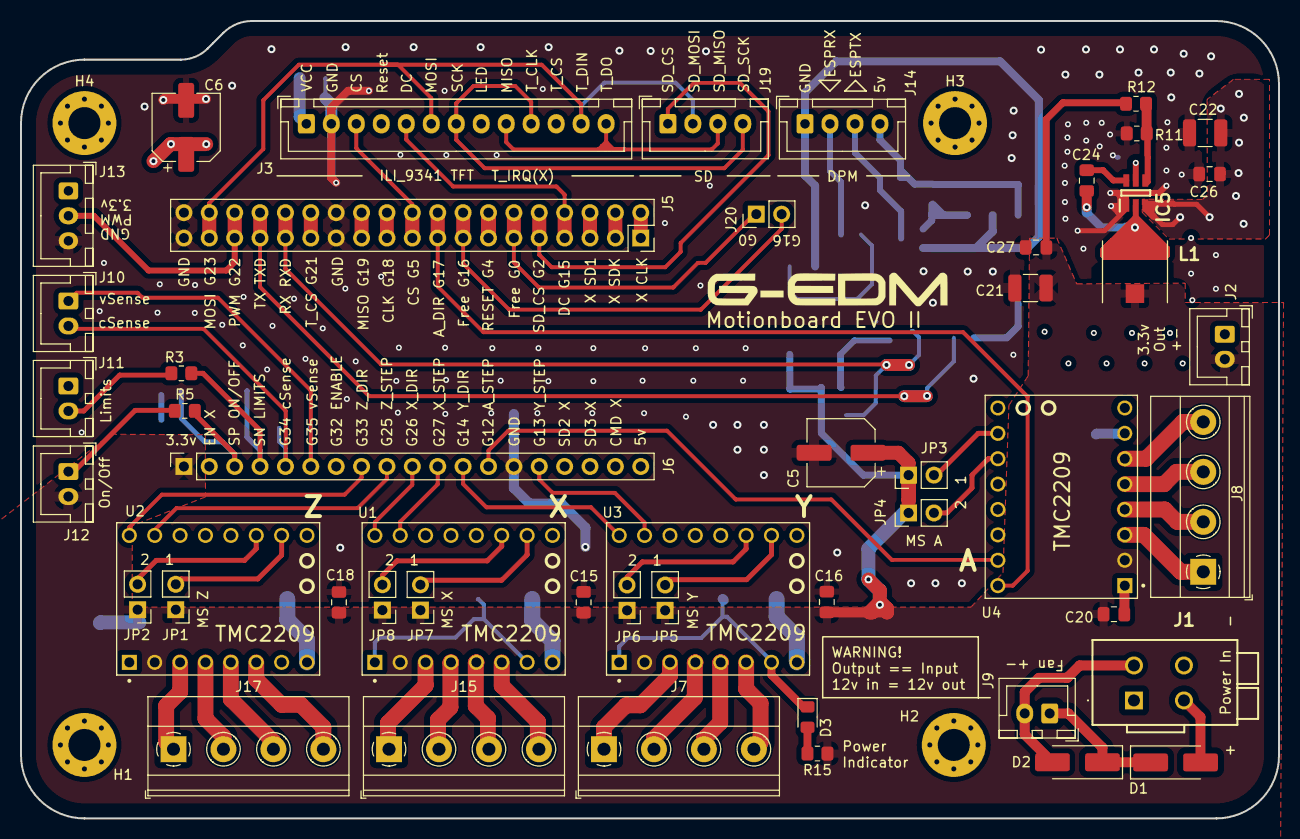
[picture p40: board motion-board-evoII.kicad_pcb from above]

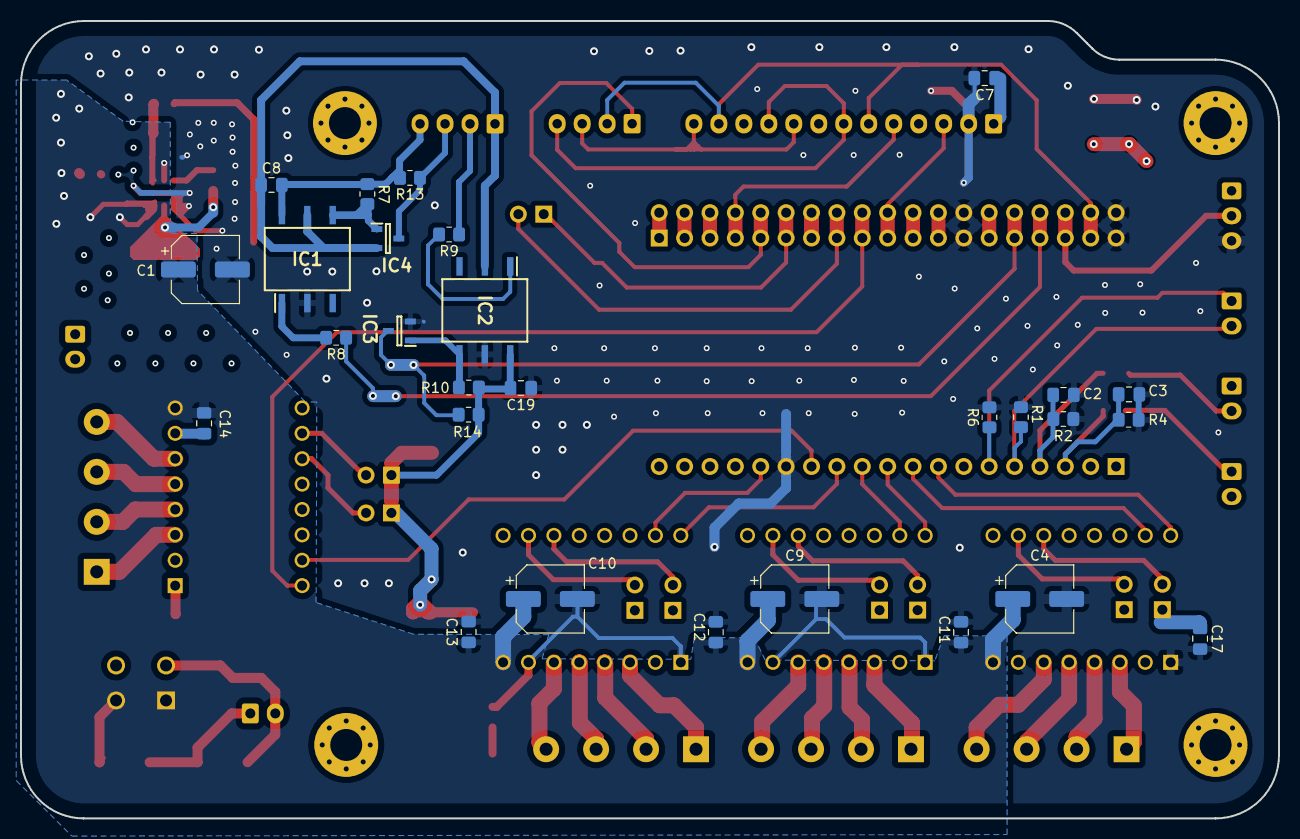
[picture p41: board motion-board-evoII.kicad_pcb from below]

Board: 4 copper layers, 125.9 x 79.8 mm, 82 parts (28 on the bottom side), 71 nets.

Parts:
C1, C4, C9, C10: 100uf35v-6.3x7.7mm (EEE-HA1V101XP); CP_Elec_6.3x7.7
C2, C3, C7, C8, C11, C12, C13, C14, C15, C16, C17, C18, C19, C20, C24, C26, C27: 0.1uf-50v-x7r; C_0805_2012Metric_Pad1.18x1.45mm_HandSolder
C5, C6: 220uf16v-6.3x7.7mm (EEE-HA1C221XP); CP_Elec_6.3x7.7
C21: 22uf-16v-X7R (GRM32ER71C226KEA8K); C_1210_3225Metric_Pad1.33x2.70mm_HandSolder
C22: 4.7uf-50v-X7R (GRM32ER71H475KA88L); C_1210_3225Metric_Pad1.33x2.70mm_HandSolder
D1, D2: 60v3ASchottky; D_SMA_Handsoldering
D3: 597-3305-607F; LED_0805_2012Metric_Pad1.15x1.40mm_HandSolder
H1: MountingHole_Pad; MountingHole_3.2mm_M3_Pad_Via
H2, H3, H4: MountingHole; MountingHole_3.2mm_M3_Pad_Via
IC1, IC2: H11L1SR2M_F132; SOT254P916X480-6N
IC3, IC4: MMBT3904; SOT95P240X110-3N
IC5: LMR51420XFDDCR; SOT95P280X110-6N
J1: WAGO 2601-1102; 26011102
J2, J9, J10, J11, J12: JST XHP-2; JST_XH_B2B-XH-A_1x02_P2.50mm_Vertical
J3: JST XHP-13; JST_XH_B13B-XH-A_1x13_P2.50mm_Vertical
J5: 2,54mm pin socket 2x19; PinSocket_2x19_P2.54mm_Vertical
J6: 2,54mm pin socket 1x19; PinSocket_1x19_P2.54mm_Vertical
J7, J8, J15, J17: 35° 4-pole screw terminal ( TE Connectivity 79668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; TerminalBlock_Phoenix_MKDS-1,5-4_1x04_P5.00mm_Horizontal
J13: JST XHP-3; JST_XH_B3B-XH-A_1x03_P2.50mm_Vertical
J14, J19: JST XHP-4; JST_XH_B4B-XH-A_1x04_P2.50mm_Vertical
J20: SDI_T_DIN_SD_MOSI; PinHeader_1x02_P2.54mm_Vertical
JP1, JP2, JP3, JP4, JP5, JP6, JP7, JP8: 1x02 pin header with low profilejumper cap (149-3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; PinHeader_1x02_P2.54mm_Vertical
L1: 7447786008 2.3A 8.2uh; WE-PD_6033_6050_PLASTIC_BASE54
R1, R2, R4, R6: 100k; R_0805_2012Metric_Pad1.20x1.40mm_HandSolder
R3, R5: 1k; R_0805_2012Metric_Pad1.20x1.40mm_HandSolder
R7, R10, R14: 470; R_0805_2012Metric_Pad1.20x1.40mm_HandSolder
R8, R13: E330; R_0805_2012Metric_Pad1.20x1.40mm_HandSolder
R9: E499; R_0805_2012Metric_Pad1.20x1.40mm_HandSolder
R11: 22.1k 1% Würth WRIS-RSKS 560112120026; R_0805_2012Metric_Pad1.20x1.40mm_HandSolder
R12: 100k 1%; R_0805_2012Metric_Pad1.20x1.40mm_HandSolder
R15: 220; R_0805_2012Metric_Pad1.20x1.40mm_HandSolder
U1, U2, U3, U4: TMC2209; MODULE_TMC2209_SILENTSTEPSTICK

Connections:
3.3v+: C5.1, C6.1, C7.1, C15.1, C16.1, C17.1, C18.1, C19.2, C20.1, C21.2, C27.2, IC2.6 (VCC), J2.2, J3.1, J3.8, J6.1, J11.1, J12.2, J13.1, JP1.1 (A), JP2.1 (A), JP3.1 (A), JP4.1 (A), JP5.1 (A), JP6.1 (A), JP7.1 (A), JP8.1 (A), L1.2, R10.1, R12.1, R14.2, R15.1, U1.2 (VIO), U2.2 (VIO), U3.2 (VIO), U4.2 (VIO)
12v+: C1.1, C4.1, C9.1, C10.1, C11.1, C12.1, C13.1, C14.1, C22.2, C26.2, D1.2 (A), IC5.3 (VIN), IC5.5 (EN), J1.1 (1.1), J1.2 (1.2), U1.8 (VM), U2.8 (VM), U3.8 (VM), U4.8 (VM)
CLK: J3.7, J3.10, J5.21, J5.22, J19.4
CS: J3.3, J5.19, J5.20
DC: J3.5, J5.7, J5.8
DPMRXB: IC4.3 (COLLECTOR), J14.3, R13.1
DPMTXB: J14.2, R9.1
GND: C1.2, C2.2, C3.2, C4.2, C5.2, C6.2, C7.2, C9.2, C10.2, C11.2, C12.2, C13.2, C14.2, C15.2, C16.2, C17.2, C18.2, C19.1, C20.2, C21.1, C22.1, C26.1, C27.1, D2.2 (A), D3.1 (K), IC1.2 (CATHODE), IC2.5 (GND), IC3.2 (EMITTER), IC5.1 (GND), J1.3 (2.1), J1.4 (2.2), J2.1, J3.2, J5.25, J5.26, J5.37, J5.38, J6.14, J9.2, J13.3, R1.2, R2.2, R4.2, R6.2, R11.2, U1.1 (GND), U1.7 (GND), U2.1 (GND), U2.7 (GND), U3.1 (GND), U3.7 (GND), U4.1 (GND), U4.7 (GND)
GND5v: C8.1, IC1.5 (GND), IC2.2 (CATHODE), IC4.2 (EMITTER), J14.1
GPIO16: J5.15, J5.16, J20.2
Limit39: C2.1, J6.4, R2.1, R3.2
MOSI: J3.6, J3.12, J5.35, J5.36, J19.2
Miso: J3.9, J3.13, J5.23, J5.24, J19.3
unnamed: D1.1 (K), D2.1 (K), J9.1
unnamed: D3.2 (A), R15.2
unnamed: IC1.1 (ANODE), R8.2
unnamed: IC1.4 (VO), IC4.1 (BASE), R7.2
unnamed: IC2.1 (ANODE), R9.2
unnamed: IC2.4 (VO), IC3.1 (BASE), R10.2
unnamed: C24.1, IC5.6 (CB)
unnamed: IC5.4 (FB), R11.1, R12.2
unnamed: C24.2, IC5.2 (SW), L1.1
unnamed: J5.1, J5.2
unnamed: J5.3, J5.4
unnamed: J5.5, J5.6
unnamed: J7.1, U3.3 (M1B)
unnamed: J7.2, U3.4 (M1A)
unnamed: J7.3, U3.5 (M2A)
unnamed: J7.4, U3.6 (M2B)
unnamed: J8.1, U4.3 (M1B)
unnamed: J8.2, U4.4 (M1A)
unnamed: J8.3, U4.5 (M2A)
unnamed: J8.4, U4.6 (M2B)
unnamed: J11.2, R3.1
unnamed: J12.1, R5.1
unnamed: J15.1, U1.3 (M1B)
unnamed: J15.2, U1.4 (M1A)
unnamed: J15.3, U1.5 (M2A)
unnamed: J15.4, U1.6 (M2B)
unnamed: J17.1, U2.3 (M1B)
unnamed: J17.2, U2.4 (M1A)
unnamed: J17.3, U2.5 (M2A)
unnamed: J17.4, U2.6 (M2B)
PWM: J5.33, J5.34, J13.2
RX(IO3): IC3.3 (COLLECTOR), J5.29, J5.30, R14.1
SD_CS: J5.9, J5.10, J19.1
Start36: C3.1, J6.3, R4.1, R5.2
TX(IO1): J5.31, J5.32, R8.1
T_CS: J3.11, J5.27, J5.28
VCCB: C8.2, IC1.6 (VCC), J14.4, R7.1, R13.2
adir17: J5.17, J5.18, U4.9 (DIR)
ams1: JP3.2 (B), U4.15 (MS1)
ams2: JP4.2 (B), U4.14 (MS2)
astep12: J6.13, U4.10 (STEP)
enable-all: J6.7, U1.16 (~EN), U2.16 (~EN), U3.16 (~EN), U4.16 (~EN)
gpio0: J5.11, J5.12, J20.1
input35: J6.6, J10.1, R6.1
reset: J3.4, J5.13, J5.14
vSense34: J6.5, J10.2, R1.1
xdir: J6.10, U1.9 (DIR)
xms1: JP7.2 (B), U1.15 (MS1)
xms2: JP8.2 (B), U1.14 (MS2)
xstep: J6.11, U1.10 (STEP)
ydir: J6.12, U3.9 (DIR)
yms1: JP5.2 (B), U3.15 (MS1)
yms2: JP6.2 (B), U3.14 (MS2)
ystep: J6.15, U3.10 (STEP)
zdir: J6.8, U2.9 (DIR)
zms1: JP1.2 (B), U2.15 (MS1)
zms2: JP2.2 (B), U2.14 (MS2)
zstep: J6.9, U2.10 (STEP)

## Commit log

2024-06-12 Add files via upload
    3/4" water outlet for two M10 fittings to connect the wire module.
    [water-flow-nozzle-dual-hose-34.stl]
2024-06-12 main wire module v4 - enlarged pockets for slide bushings
    The pockets for the v1-3 wire module are very tight and getting the slide bushings in required heavy heating and was just not worth the trouble. Enlarged the pockets a little for v4.
    [15x6x5bearing-to-30mm-vgroove.stl, TPU-nozzle-sealring.stl, flushing-nozzle.stl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]
2024-06-13 Small changes on some screw pockets and bigger holes for the slide bushings
    [15x6x5bearing-to-30mm-vgroove.stl, TPU-nozzle-sealring.stl, flushing-nozzle.stl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]
2024-06-30 Added current contact mount
    [tmp-current-contact-mount.stl]
2024-08-08 Added tech drawings for the portal plate
2024-08-13 Added schmeatics for the pulseboard EVO²
    Check the readme first. It is just the pulseboards schematics without the sensing circuit.
2024-08-27 Added motionboard schematics
2024-09-09 uploaded all gerber files, schematics and kicad projects
    [evo-cube-pulseboard-B_Courtyard.gbr, evo-cube-pulseboard-B_Cu.gbl, evo-cube-pulseboard-B_Mask.gbs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]
2024-10-09 A little stronger
    [tmp-current-contact-mount-v2.stl]
2024-11-12 New panel
    Slightly changed the panel to add a switch on the side.
    [EVOII-panel-ref2-DPM-buttons.stl, EVOII-panel-ref2.stl]
